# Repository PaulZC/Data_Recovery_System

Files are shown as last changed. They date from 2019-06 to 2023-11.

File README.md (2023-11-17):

# Data_Recovery_System

### ! Still Work In Progress - but more complete than it was !

This is the repository for the SuperBIT Data Recovery System (a.k.a. the data drop capsule).

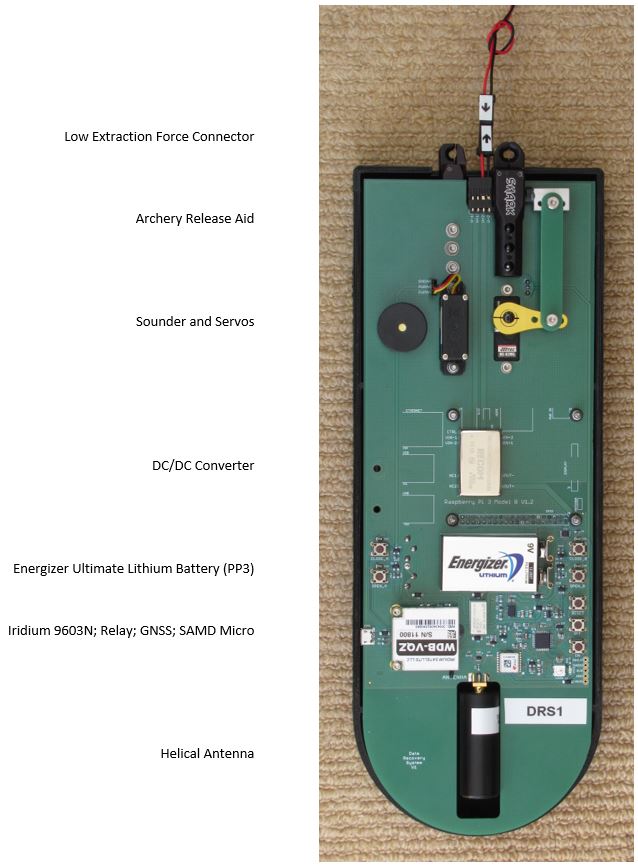
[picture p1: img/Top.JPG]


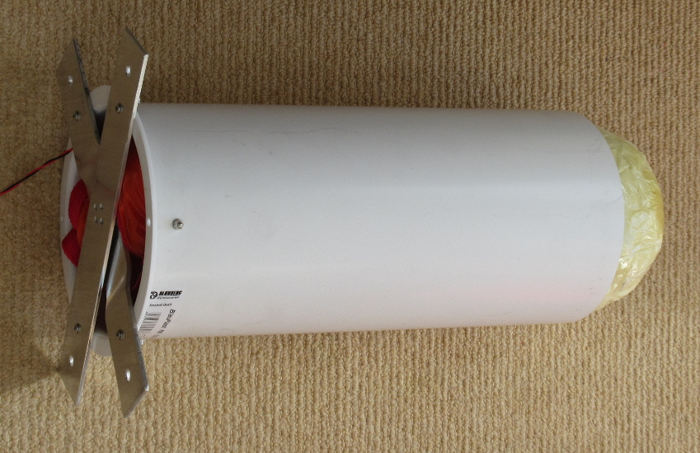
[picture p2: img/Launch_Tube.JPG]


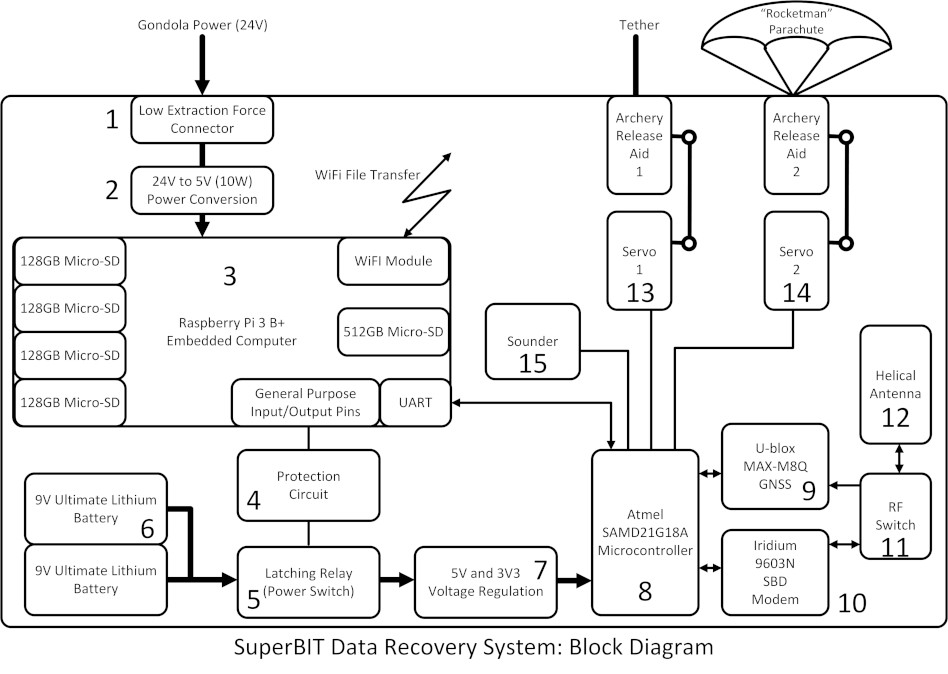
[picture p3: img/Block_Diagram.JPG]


The DRS comprises:
- Raspberry Pi equipped with: 1 x 512GB and 4 x 128GB (RAID1) SD data storage
- ATSAMD21G18 microcontroller as used on the Adafruit Feather M0 Adalogger and the Arduino Zero
- [u-blox MAX-M8Q GNSS receiver](https://www.u-blox.com/en/product/max-m8-series)
- Iridium 9603N Short Burst Data modem
- Maxtena M1600HCT-P-SMA antenna, shared via a Skyworks AS179-92LF RF switch
- two [servo-actuated](https://www.servoshop.co.uk/index.php?pid=HITHS82MG&area=Servo)
[Scott Archery release aids](https://scottarchery.com/collections/releases/products/shark-release): one for the tether and one for the parachute
- [Rocketman 4' parachute](https://the-rocketman.com/recovery-html/)
- Low extraction force power connector
- 3D-printed cover
- PU foam enclosure
- PVC launch tube

See [LEARN.md](./LEARN.md) for more details.

[PCB.md](./PCB.md) contains instructions on how to populate and test the PCB.

[PI.md](./PI.md) contains instructions on how to configure the Raspberry Pi.

[ASSEMBLY.md](./ASSEMBLY.md) contains instructions on how to prepare the DRS for flight.

[GoGoGo.md](./GoGoGo.md) contains instructions on how to release and track the DRS.

The schematic, PCB layout and Bill Of Materials can be found in [Data_Recovery_System_V1.pdf](./Data_Recovery_System_V1.pdf)

The BOM is also available in [Excel .xlsx format](./Data_Recovery_System_BOM.xlsx)

The [Eagle](./Eagle) directory contains the schematic and pcb design files.

The [Arduino](./Arduino) directory contains the Arduino code for the SAMD microcontroller.

The [Drawings](./Drawings) directory contains the drawings for the trigger linkage.

The [OpenSCAD](./OpenSCAD) directory contains the OpenSCAD and STL files for the 3D-printed cover, release crown/mount, and heatsink.

The Python software tools which need to be installed on the Raspberry Pi can be found the [DRS_Python_Tools repo](https://github.com/PaulZC/DRS_Python_Tools).

See [SERVO.md](./SERVO.md) for details on how to modify the HiTec servo for
high altitude operation.

See [SHARK.md](./SHARK.md) for details on how to modify the Scott Archery Shark release aid.

## Licence

This project is distributed under a Creative Commons Attribution + Share-alike (BY-SA) licence.
Please refer to section 5 of the licence for the "Disclaimer of Warranties and Limitation of Liability".

Enjoy!

**_Paul_**

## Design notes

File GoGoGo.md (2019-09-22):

# GoGoGo

Instructions on how to enable, release and track the DRS.

Also included are [instructions](https://github.com/PaulZC/Data_Recovery_System/blob/master/GoGoGo.md#step-10-resetting-the-microcontroller) on how to reset the microcontroller from 'Gone' mode into 'Waiting for GoGoGo' mode (required after performing a drop / test drop).

## Prerequisites

- The DRS should have been prepared following the instructions in [ASSEMBLY.md](https://github.com/PaulZC/Data_Recovery_System/blob/master/ASSEMBLY.md)
- The Raspberry Pi should have been configured for SuperBIT WiFi and have the [DRS_Python_Tools](https://github.com/PaulZC/DRS_Python_Tools) installed following the instructions in [PI.md](https://github.com/PaulZC/Data_Recovery_System/blob/master/PI.md)
- The SAMD microcontroller should have been programmed with the correct Arduino code; the servo open/close positions set and the latching relay set OFF (which is only possible while the Pi is powered)
- The microcontroller code should have been freshly installed. If a test drop has been performed, the code needs to be 'reset' either by re-uploading the code or by following the [instructions below](https://github.com/PaulZC/Data_Recovery_System/blob/master/GoGoGo.md#step-10-resetting-the-microcontroller)

## Step 1: Apply power

- Apply 24V DC power to the DRS via the 2-pin low extraction force connector. The Recom REC10-2405SRWZ/H3/A/M DC-DC converter can operate from 9V to 36V. (A 48V version is available which can operate from 18V to 75V)
- The Raspberry Pi will boot up and attempt to connect to WiFi: SSID SuperBIT with PSK Timmins2019

## Step 2: Log in using SSH

- Connect to the Pi using SSH. Log in as user 'pi' with password 'raspberry'

## Step 3: File transfer

- Transfer files onto the Pi's /mnt/raid1 RAID storage using SFTP

## Step 4: Power up the microcontroller

- A few minutes before the chosen drop time, use the SSH console to cd into the DRS_Python_Tools directory
- Power up the microcontroller by running the script 'DRS_on.py': python DRS_on.py
- The script sets three of the Pi's GPIO pins into the correct state to set the Omron latching relay, switching on 9V battery power to the microcontroller
- The microcontroller will power up and will start to establish a GNSS fix

## Step 5: Check the GNSS fix status

- The NMEA messages from the u-blox MAX-M8Q GNSS receiver are echoed by the microcontroller to the Pi's serial port
- Run the script 'DRS_log_serial.py' from the SSH console: python DRS_log_serial.py
- The script runs for 5 seconds and will append the incoming serial data to DRS_serial_log.txt. The script then displays the tail of the log file
- Look at the lines containing GPGGA. If the GNSS has achieved a fix, you should see the correct date, time, latitude and longitude
- If you only see the correct time, the GNSS receiver has locked onto at least one satellite but has not yet established a fix
- If the GNSS has not established a fix, decide whether to wait for a fix or whether to drop anyway (hoping that the GNSS will establish a fix during the descent - it should!)

## Step 6: Drop

- 30 seconds before the desired drop time, run the script 'DRS_GoGoGo.py': python DRS_GoGoGo.py
- The script will append any incoming GNSS serial data to DRS_serial_log.txt for three seconds; the script then displays the tail of the log file
- The script then sends a GoGoGo command to the microcontroller via the serial port
- The script then shuts down the Pi (sudo shutdown now)
- The microcontroller will wait 30 seconds and then open archery release A
- The sounder will start to beep every 5 seconds

## Step 7: During the descent

- The DRS will fall, pulling apart the power connection (disconnecting power to the Pi)
- The parachute will unfurl but will remain attached to archery release B
- The microcontroller is now in 'Gone' mode
- The microcontroller will obtain a GNSS fix and send this as an Iridium Short Burst Data message every 2 minutes
- Messages will be delivered via email to the addresses configured in the Rock7 Operations Delivery Groups
- The message interval can be changed by logging in to RockBLOCK Operations (https://rockblock.rock7.com/Operations) (ask Paul for the username and password) and using the 'Send a Message' option
- Send a message to the RockBLOCK (DRS1 is RockBLOCK 11800) containing the text: [INTERVAL=nn]
- where nn is the message interval in minutes. The square brackets are important
- If you want to try this as a test, make sure you do it outdoors where the DRS has a clear view of the sky
- The [Iridium_9603_Beacon webpage](https://github.com/PaulZC/Iridium_9603_Beacon/blob/master/RockBLOCK.md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) provides extra information

## Step 8: After landing

- Once you have confirmed that the DRS has landed, you can release it from the parachute via an Iridium message
- Send a message containing the text: [PARACHUTE=hh:mm]
- where hh and mm are the current **UTC** time. The square brackets are important
- The microcontroller will ignore the message if hh and mm do not match current UTC time to +/- 15 minutes. This ensures any old queued messages are ignored
- The microcontroller will open archery release B after the next SBD message cycle

## Step 9: Other commands

- If you wish to disable the sounder / beeper, send the message: [SOUNDER_OFF]
- The sounder can be re-enabled with the message: [SOUNDER_ON]
- The DRS can also be configured to forward all messages to another RockBLOCK using the message: [RBDESTINATION=nnnnn]
- where nnnnn is the RockBLOCK serial number (not the IMEI) of the 9603N you wish the messages to be forwarded to
- Full details can be found on the [Iridium_9603_Beacon webpage](https://github.com/PaulZC/Iridium_9603_Beacon/blob/master/RockBLOCK.md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)
- The recovery team could use this to track the DRS and release the parachute from anywhere - [without an internet connection](https://github.com/PaulZC/Iridium_9603_Beacon/blob/master/RockBLOCK.md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)

## Step 10: Resetting the microcontroller

- Once the microcontroller has received a 'GoGoGo' message, a 'Gone' flag is set in flash memory. Resetting the microcontroller or disconnecting and reconnecting the batteries does not clear the flag
- To reset the microcontroller into 'Waiting for Go' mode: press and hold the OPEN_A, CLOSE_A, OPEN_B and CLOSE_B buttons, then press and release the RESET button
- Keep the OPEN_A, CLOSE_A, OPEN_B and CLOSE_B buttons pressed down until the NeoPixel goes green, then release them
- The 'Gone' flag is now clear. The microcontroller returns to [Step 5](https://github.com/PaulZC/Data_Recovery_System/blob/master/GoGoGo.md#step-5-check-the-gnss-fix-status)

## Step 11: Resetting the latching relay

- Resetting the latching relay can only be done while the Pi is powered
- Connect the DRS to 24V using the power pins
- The OFF button can then be pressed which resets (opens) the latching relay contacts
- To be kind to the Pi, SSH in over WiFi or Ethernet and 'sudo shutdown now' before disconnecting the power

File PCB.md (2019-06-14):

# PCB Assembly

This guide contains instructions on how to assemble the DRS PCB: starting with the bare PCB and finishing with a populated PCB which has been tested with test code.

### Blank PCB

Start by having the blank PCBs manufactured. If you are based in the UK or Europe, I can recommend
[Multi-CB](https://www.multi-circuit-boards.eu/en/index.html) who can manufacture PCBs in 1-8 working days and
can process the Eagle .brd file direct - there's no need to generate Gerber files.

You will find the PCB and paste stencil design files in the [Eagle directory](https://github.com/PaulZC/Data_Recovery_System/tree/master/Eagle)

The PCB and trigger linkage pieces are incorporated into a single board. The design includes two score lines which Multi-CB
will machine into the board if you ask them to, allowing the trigger linkage pieces to be easily snapped off.

My recommended options are:
- Layers: 4 layers
- Format: Panel
- Panel Type: Multiplier
- Mechanical treatment: Milled and Scored
- Panelization: Yes, by Multi-CB
- Panel size (x/y): 128.27 X 304.8 mm
- Piece size (x/y): 128.27 X 304.8 mm
- PCBs / x-, y-Axis: 1 X 1 Pieces
- Surface finish: Chemical gold (ENIG)
- Material: FR4, 1.55mm
- Cu layers: 35um
- Solder stop: both sides, green
- Marking print: both sides, white
- **Comments: PCB includes two score lines. VSCORE data is in layer 148**

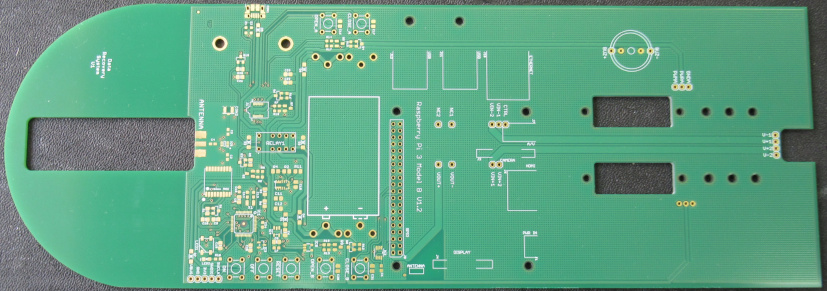
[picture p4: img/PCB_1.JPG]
PCB_1


### Add solder paste

Multi-CB can also provide you with a solder paste (SMD) stencil for the PCB. The [Eagle directory](https://github.com/PaulZC/Data_Recovery_System/tree/master/Eagle)
contains a separate design for the paste stencil which is 10mm wider than the DRS PCB, to allow you to fix it down with tape.

My recommended options are:
- SMD stencil for: top layer
- Size (x/y): 118.11 X 88.9 mm
- Type: custom
- Pad reduction: yes, 10%
- Thickness: 100um
- Existing fiducials: lasered through
- Text type: half lasered
- Double-sided brushing: yes

Secure the blank PCB onto a flat work surface by locating it between two engineer's squares. I use a sheet of toughened glass
as the work surface as it is both very flat and easy to clean.

Use the two round fiducials to line up the stencil with the PCB. Secure the stencil with tape.

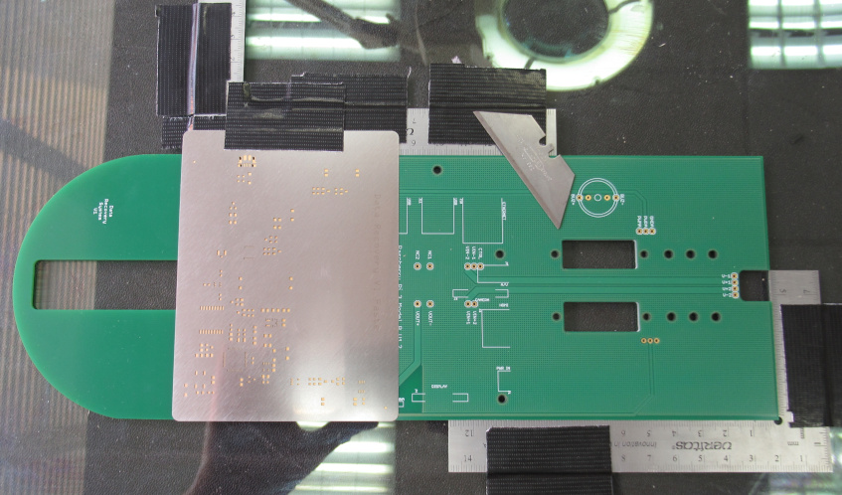
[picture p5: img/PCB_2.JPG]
PCB_2


Apply solder paste close to the component cut-outs and then scrape the paste over the stencil using a knife blade
or a similar straight edge. Take appropriate safety precautions when working with solder paste - particularly if you are using
tin-lead solder instead of lead-free.

### Position the surface mount components

Position the components onto the blobs of solder paste using tweezers. A magnifier lamp or a USB microscope will
help you place the components in the correct position. J1 - the 20-way Samtec connector - is probably the trickiest
component to position. Take extra time to make sure the legs are centered accurately on the pads.

### Reflow the surface mount components

Use a reflow oven to heat the circuit board to the correct temperatures to melt the solder. A reflow oven doesn't need to be
expensive. The one shown below was assembled from:

- Quest 9L 800W mini-oven
- Inkbird PID temperature controller and 40A solid state relay
- Type K thermocouple

Several people have published good reflow oven construction guides, including [this one](http://tt7hab.blogspot.com/2018/06/the-reflow-oven.html) and [this one](http://www.die4laser.com/toaster/index.html).

V5_Assembly_8

Use the correct temperature profile for your solder paste, but you won't go far wrong with 160C for four minutes, followed by
210C for one minute, followed by a cool-down with the door open. Use a flashlight to check that the solder has melted across
the whole PCB at 210C. Hold the temperature at 210C a little longer if some of the solder paste still appears 'gray' instead of 'silver'.

### Check for shorts

Carefully examine all the solder joints and correct any shorts you find.

The 'trick' to removing a short is to add more solder or solder paste and then to use
copper solder braid or wick to remove all the solder in one go.

Shorts_1

Shorts_2

Shorts_3

Use a cotton bud (q-tip) dipped in Iso-Propyl Alcohol (IPA / Propanol / rubbing alcohol) to remove any flux residue.

All being well, your PCB should look like this:

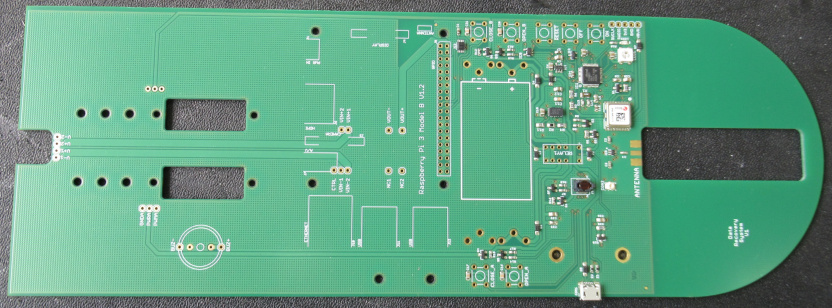
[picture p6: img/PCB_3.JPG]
PCB_3


### Press-in nuts

The Iridium 9603N module is held in place by two 2-56 screws. The threaded 2-56 press-in nuts now need to be pressed into the rear of the
PCB. These are McMaster part number 95117A411. The nuts are best pressed into place using an arbor press.

### Add the non-surface mount components

The non-surface mount components (battery clips, relay, switches, SMA conector, DC-DC converter, sounder 3-pin servo headers, 4-pin power header) can now be soldered in by hand.

### Install the bootloader

The SAMD21G18A processor now needs to be configured with a bootloader using a J-Link programmer or similar, connecting it to the five pads on the right hand edge of the PCB.
Full details are included in the [Iridium_9603_Beacon repo](https://github.com/PaulZC/Iridium_9603_Beacon/blob/master/LEARN.md#how-do-i-install-the-atsamd21g18-bootloader).

### Test the PCB

Before connecting the Iridium 9603N, it is a good idea to test the completed PCB. The [Arduino](https://github.com/PaulZC/Data_Recovery_System/tree/master/Arduino)
directory contains a sketch called Data_Recovery_System_V1_Test.ino which will test all of the components on the PCB for you. Messages are displayed
on the Arduino IDE Serial Monitor as each test is passed.

### Install the Iridium 9603N module

Take appropriate ESD precautions throughout and especially when handling the 9603N module.

Connect the 9603N to the beacon PCB using a HIROSE (HRS) u.FL-u.FL cable or similar. The cable needs to be 50 Ohm and approximately 25mm long.

Carefully fold the 9603N module over onto the PCB, insert the 20-way connector into the Samtec socket, then secure the module using:
- two 4.5mm OD x 6mm spacers (McMaster 94669A100)
- two 2-56 x 7/16" screws (McMaster 92185A081)

Screw the GNSS+Iridium antenna onto the SMA connector

### Retest the PCB

Now that the 9603N has been installed, retest the completed PCB using the [Arduino test code](https://github.com/PaulZC/Data_Recovery_System/tree/master/Arduino/Data_Recovery_System_V1_Test).

### Secure J1 with Epoxy

I recommend securing J1 to the PCB with a small amount of epoxy to make it more robust. 3M Scotch-Weld 2216 is an ideal choice as it remains slightly flexible when cured.
You will need to temporarily remove the 9603N while you apply the epoxy. Apply the mixed epoxy around the body and legs of J1 using a toothpick,
taking great care to keep the epoxy clear of the connector opening and pins. Make sure the epoxy is fully cured before re-installing the 9603N.

### Lacquer the PCB

I recommend giving the PCB a coat of lacquer. You will need to temporarily remove the 9603N while you apply the lacquer. Cover all of the surface mount components with
[Acrylic Protective Lacquer (conformal coating)](https://uk.rs-online.com/web/p/conformal-coatings/3217324/) avoiding J1, CON1, CON2, the switches and IO pads.

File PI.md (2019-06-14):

# Raspberry Pi Configuration

This guide contains instructions on how to configure the Raspberry Pi for use on the DRS.

1. Burn the latest Raspberry Pi Raspbian onto the 512GB micro SD card
- Visit https://www.raspberrypi.org/downloads/
- Download the latest "Raspbian Stretch with desktop and recommended software"
- Extract the .img with e.g. http://www.7-zip.org/download.html
- Burn it to the SD card using e.g. https://sourceforge.net/projects/win32diskimager/

2. Insert the SD card into a Raspberry Pi 3 B+
- Connect screen, mouse, keyboard and (finally) power

3. Let the Pi boot. It will automatically resize the SD card file system to its full size

4. Go through the set up process to set the country and connect to a WiFi network

5. Skip the update software step (we’ll be doing an update and upgrade shortly)

6. Let the Pi restart if requested

7. Open a terminal window by clicking on the >_ icon

8. In  the terminal window:
- sudo raspi-config
- Select option2 then option N1 to change the hostname to e.g. drs1
- Select option 3 then option B1 then option B2 to boot into “Console Autologin”
- Select option 4 then option I4 to change the WiFi country if required
- Select option 5 then option P2, select Yes to enable the SSH server
- Select option 5 then option P6, select No for the login shell over serial, then select Yes to enable the hardware serial port
- Select finish and reboot the Pi

9. After the reboot, you should be presented with a console prompt (e.g.) pi@drs1

10. (You can start an X session if you want to using startx)

11. Remove Wolfram and LibreOffice to free up some storage space
- sudo apt-get purge wolfram-engine
- sudo apt-get clean
- sudo apt-get autoremove
- sudo apt-get remove --purge libreoffice*
- sudo apt-get clean
- sudo apt-get autoremove

12. Update and upgrade raspbian
- sudo apt-get update
- sudo apt-get upgrade

13. If you want to change WiFi networks from the console, you can do this by editing wpa_supplicant.conf
- sudo nano /etc/wpa_supplicant/wpa_supplicant.conf

14. Make a note of the Pi’s wireless (wlan0) IP number (hopefully it won’t change when you reboot)
- ifconfig -a

15. Shutdown the Pi
- sudo shutdown now

16. Wait until the green LED stops blinking, then remove the power

17. Disconnect the screen, keyboard and mouse

18. Install the four 128GB micro-SD cards in their miniature USB adapters

19. Power the Pi and you should see LEDs light up on all four micro-SD adapters

20. Connect to the Pi over SSH using (e.g.) PuTTY
- https://www.chiark.greenend.org.uk/~sgtatham/putty/latest.html
- Log in as user pi with the password raspberry (unless you changed it!)

21. Run lsblk and check that you now have four drives called sda, sdb, sdc and sdd. (The 512GB card is called mmcblk0)

22. Create a RAID-1 system following the instructions in section 3 of:
- https://blog.alexellis.io/hardened-raspberry-pi-nas/ 
- sudo fdisk /dev/sda
- o
- n
- p
- enter (default)
- enter (default)
- enter (default)
- w
- sudo fdisk /dev/sdb
- o
- n
- p
- enter (default)
- enter (default)
- enter (default)
- w
- sudo fdisk /dev/sdc
- o
- n
- p
- enter (default)
- enter (default)
- enter (default)
- w
- sudo fdisk /dev/sdd
- o
- n
- p
- enter (default)
- enter (default)
- enter (default)
- w
- sudo apt-get -qy install mdadm
- sudo mdadm --create --verbose /dev/md0 --level=mirror --raid-devices=4 /dev/sda1 /dev/sdb1 /dev/sdc1 /dev/sdd1
- y
- sudo mkdir -p /mnt/raid1
- sudo mkfs.ext4 /dev/md0
- sudo mount /dev/md0 /mnt/raid1/
- echo "/dev/md0  /mnt/raid1/ ext4 defaults,noatime 0 1" | sudo tee -a /etc/fstab
- sudo mdadm --detail --scan | sudo tee -a /etc/mdadm/mdadm.conf
- sudo reboot

23. Let the Pi reboot then connect again with PuTTY

24. Check that the RAID drive is ok
- df /mnt/raid1
- should return something like:
- Filesystem     1K-blocks     Used    Available Use% Mounted on
- /dev/md0       122317432 61464 115999484   1% /mnt/raid1

25. When we mount the Pi onto the DRS, it is going to be difficult to connect either screen, mouse and keyboard or to go in over WiFi (if you need to connect to a new WiFi network). So, we’ll set up a static IP address and DHCP server on the Ethernet port so we can SSH in through that. Your WiFi is probably using 192.168.0.n addresses, so we’ll use 192.168.1.n addresses for Ethernet
- sudo nano /etc/dhcpcd.conf
- uncomment and change the two lines below “Example static IP configuration:”
- interface eth0
- static ip_address=192.168.1.2/24
- ctrl-x
- y
- enter

26. Install dnsmasq:
- sudo apt-get install dnsmasq

27. Create a new dnsmasq.conf file:
- sudo mv /etc/dnsmasq.conf /etc/dnsmasq.conf.orig
- sudo nano /etc/dnsmasq.conf
- interface=eth0
- dhcp-range=192.168.1.3,192.168.1.20,255.255.255.0,24h
- ctrl-x
- y
- enter

28. Reload dnsmasq:
- sudo systemctl reload dnsmasq

29. Check the Ethernet connection by SSH-ing in over Ethernet. The Pi is 192.168.1.2

30. Download the Python tools which will enable the Arduino part of the DRS, copy the incoming GNSS serial data to DRS_serial_log.txt, and tell the DRS to “GoGoGo”:
- git clone https://github.com/PaulZC/DRS_Python_Tools

31. We now need to make DRS_Python_Tools/DRS_tx_off.py run on startup to correct Paul’s booboo. The serial Tx pin can provide just enough power to try and start the SAMD processor. DRS_tx_off.py prevents this by making the Tx pin low. DRS_on.py has to put the Tx pin back into alt5 mode before we can use the serial port again.
- sudo nano /etc/profile
- scroll to the end of the file and add
- sudo python /home/pi/DRS_Python_Tools/DRS_tx_off.py
- ctrl-x
- y
- enter

32. Shutdown the Pi. Disconnect the power once the green LED has stopped flashing. The LEDs on the four micro-SD card adapters should also stop flashing.
- sudo shutdown now

33. You can now bolt the Pi to the DRS circuit board.

The [DRS_Python_Tools repo](https://github.com/PaulZC/DRS_Python_Tools) contains:

**DRS_tx_off.py** pulls the Pi’s serial Tx pin low to prevent it from supplying power to the SAMD processor. This now runs automatically on boot.

**DRS_on.py** will set the latching relay so it provides power to the SAMD processor and restores the serial Tx pin to alt5 mode.

**DRS_log_serial.py** runs for 5 seconds, appends any serial data to DRS_serial_log.txt and then shows the tail of the log file so you can see if the GNSS receiver has established a fix.

**DRS_GoGoGo.py** sends the Go command to the SAMD processor. Confirm with y or Y. The drop will take place after 30 seconds (allowing time for the Pi to shutdown).

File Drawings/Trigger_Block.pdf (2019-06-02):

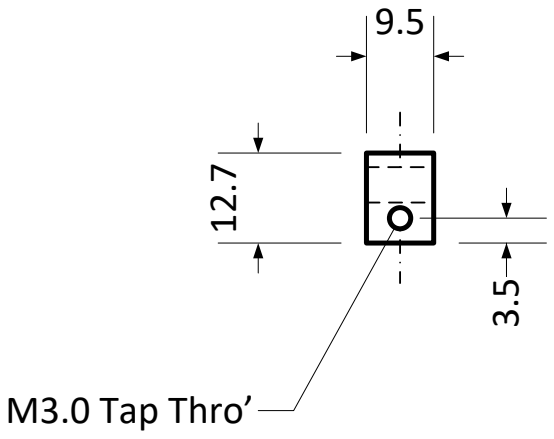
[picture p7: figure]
M3.0 Tap Thro’

Trigger Block

(Revised version for Shark and Little Goose)

Aluminium
(1/2" x 3/8" bar cut into 3/8" lengths)

Qty: 20

Ø5.0

9.5

4.5

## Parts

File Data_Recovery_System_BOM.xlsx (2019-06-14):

Part | X | Y | Angle | Package | Value | Manufacturer | Manufacturer Part No | Farnell Part No | Mouser Part No | McMaster Part No | Description | Alternative Part
Dimensions | 107.95 | 304.80 |  |  |  |  |  |  |  |  | Excludes snap-off servo linkage pieces
Fiducials - for solder paste mask alignment:
FD1 | 3.28 | 71.12 | 0 |  |  |  |  |  |  |  | Fiducial 1mm
FD2 | 102.75 | 149.86 | 0 |  |  |  |  |  |  |  | Fiducial 1mm
Surface Mount Components:
C1 | 100.2 | 141.22 | 0 | 0603 | 1uF | Walsin | 0603X105K100CT | 2496916 |  |  | MultiLayer Ceramic Capacitor; 1uF; 10V; 0603; X5R | 1uF 50V ±10% 0603 Samsung
C2 | 58.93 | 83.57 | 0 | 0603 | 120pF | Walsin | 0603B121K500CT | 2524820 |  |  | MultiLayer Ceramic Capacitor; 120pF; 50V; 0603
C3 | 49.4 | 83.57 | 180 | 0603 | 120pF | Walsin | 0603B121K500CT | 2524820 |  |  | MultiLayer Ceramic Capacitor; 120pF; 50V; 0603
C4 | 53.98 | 77.98 | 90 | 0603 | 120pF | Walsin | 0603B121K500CT | 2524820 |  |  | MultiLayer Ceramic Capacitor; 120pF; 50V; 0603
C5 | 74.8 | 88.27 | 180 | 0805 | 0.1uF | Walsin | 0805B104K500CT | 2496944 |  |  | MultiLayer Ceramic Capacitor; 0.1uF; 50V; 0805; X7R | 100nF 50V ±10% 0805 Samsung
C6 | 87.1 | 105.54 | 0 | 0805 | 10uF | Walsin | 0805F106Z100CT | 2496998 |  |  | MultiLayer Ceramic Capacitor; 10uF; 10V; 0805 | 10uF 16V ±10% 0805 Samsung
C7 | 92.75 | 102.39 | 270 | 0603 | 1uF | Walsin | 0603X105K100CT | 2496916 |  |  | MultiLayer Ceramic Capacitor; 1uF; 10V; 0603; X5R | 1uF 50V ±10% 0603 Samsung
C8 | 90.53 | 102.39 | 270 | 0805 | 10uF | Walsin | 0805F106Z100CT | 2496998 |  |  | MultiLayer Ceramic Capacitor; 10uF; 10V; 0805 | 10uF 16V ±10% 0805 Samsung
C9 | 82.2 | 79.86 | 270 | 0805 | 0.1uF | Walsin | 0805B104K500CT | 2496944 |  |  | MultiLayer Ceramic Capacitor; 0.1uF; 50V; 0805; X7R | 100nF 50V ±10% 0805 Samsung
C10 | 82.26 | 75.84 | 90 | 0805 | 10uF | Walsin | 0805F106Z100CT | 2496998 |  |  | MultiLayer Ceramic Capacitor; 10uF; 10V; 0805 | 10uF 16V ±10% 0805 Samsung
C11 | 74.4 | 102.87 | 90 | 0805 | 10nF | Walsin | 0805B103K500CT | 2496939 |  |  | MultiLayer Ceramic Capacitor; 10nF; 50V; 0805; X7R | 10nF 50V ±5% 0805 Samsung
C12 | 78.21 | 102.87 | 90 | 0805 | 10uF | Walsin | 0805F106Z100CT | 2496998 |  |  | MultiLayer Ceramic Capacitor; 10uF; 10V; 0805 | 10uF 16V ±10% 0805 Samsung
C13 | 73.03 | 93.6 | 180 | 0603 | 12pF | Walsin | 0603N120J500CT | 2496884 |  |  | MultiLayer Ceramic Capacitor; 12pF; 50V; 0603 | 12pF 50V ±5% 0603 Samsung
C14 | 73.03 | 91.31 | 180 | 0603 | 12pF | Walsin | 0603N120J500CT | 2496884 |  |  | MultiLayer Ceramic Capacitor; 12pF; 50V; 0603 | 12pF 50V ±5% 0603 Samsung
C15 | 69.19 | 109.22 | 0 | 0805 | 10uF | Walsin | 0805F106Z100CT | 2496998 |  |  | MultiLayer Ceramic Capacitor; 10uF; 10V; 0805 | 10uF 16V ±10% 0805 Samsung
C16 | 7.62 | 125.2 | 0 | 0805 | 10nF | Walsin | 0805B103K500CT | 2496939 |  |  | MultiLayer Ceramic Capacitor; 10nF; 50V; 0805; X7R | 10nF 50V ±5% 0805 Samsung
C17 | 7.62 | 137.9 | 0 | 0805 | 10nF | Walsin | 0805B103K500CT | 2496939 |  |  | MultiLayer Ceramic Capacitor; 10nF; 50V; 0805; X7R | 10nF 50V ±5% 0805 Samsung
C18 | 71.12 | 88.27 | 180 | 0603 | 1uF | Walsin | 0603X105K100CT | 2496916 |  |  | MultiLayer Ceramic Capacitor; 1uF; 10V; 0603; X5R | 1uF 50V ±10% 0603 Samsung
C19 | 91.89 | 81.69 | 0 | 0805 | 10uF | Walsin | 0805F106Z100CT | 2496998 |  |  | MultiLayer Ceramic Capacitor; 10uF; 10V; 0805 | 10uF 16V ±10% 0805 Samsung
C20 | 100.33 | 125.2 | 0 | 0805 | 10nF | Walsin | 0805B103K500CT | 2496939 |  |  | MultiLayer Ceramic Capacitor; 10nF; 50V; 0805; X7R | 10nF 50V ±5% 0805 Samsung
C21 | 100.33 | 137.9 | 0 | 0805 | 10nF | Walsin | 0805B103K500CT | 2496939 |  |  | MultiLayer Ceramic Capacitor; 10nF; 50V; 0805; X7R | 10nF 50V ±5% 0805 Samsung
C22 | 30.48 | 105.69 | 270 | 0805 | 10uF | Walsin | 0805F106Z100CT | 2496998 |  |  | MultiLayer Ceramic Capacitor; 10uF; 10V; 0805 | 10uF 16V ±10% 0805 Samsung
C23 | 27.3 | 105.69 | 270 | 0805 | 0.1uF | Walsin | 0805B104K500CT | 2496944 |  |  | MultiLayer Ceramic Capacitor; 0.1uF; 50V; 0805; X7R | 100nF 50V ±10% 0805 Samsung
C24 | 84.2 | 97.16 | 0 | 0603 | 1uF | Walsin | 0603X105K100CT | 2496916 |  |  | MultiLayer Ceramic Capacitor; 1uF; 10V; 0603; X5R | 1uF 50V ±10% 0603 Samsung
C25 | 92.71 | 92.84 | 0 | 0805 | 10uF | Walsin | 0805F106Z100CT | 2496998 |  |  | MultiLayer Ceramic Capacitor; 10uF; 10V; 0805 | 10uF 16V ±10% 0805 Samsung
C26 | 28.45 | 87.63 | 270 | 0805 | 10uF | Walsin | 0805F106Z100CT | 2496998 |  |  | MultiLayer Ceramic Capacitor; 10uF; 10V; 0805 | 10uF 16V ±10% 0805 Samsung
CON1 | 2.99 | 92.71 | 270 |  | Micro_USB | Amphenol_FCI | 10103594 | 2293752 |  |  | Amphenol FCI 10103594 Micro USB Type B | A01SB7X4X1B21-167 Micro USB 5S B
CON2 | 41.78 | 83.57 | 0 | uFL | uFL | Hirose | U.FL-R-SMT(01) | 3908021 |  |  | HIROSE U.FL-R-SMT(01); U.FL Coaxial; Straight Jack; 50 ohm
D1 | 82.18 | 105.57 | 180 | SOD-123 | MBR120 | ON SEMICONDUCTOR | MBR120VLSFT1G | 1431044 |  |  | Schottky Rectifier; 20V; 1A; SOD-123
D2 | 53.34 | 91.44 | 180 | SOD-123 | MBR120 | ON SEMICONDUCTOR | MBR120VLSFT1G | 1431044 |  |  | Schottky Rectifier; 20V; 1A; SOD-123
D3 | 53.34 | 111.76 | 180 | SOD-123 | MBR120 | ON SEMICONDUCTOR | MBR120VLSFT1G | 1431044 |  |  | Schottky Rectifier; 20V; 1A; SOD-123
D4 | 81.41 | 110.87 | 0 | SOD-123 | MBR120 | ON SEMICONDUCTOR | MBR120VLSFT1G | 1431044 |  |  | Schottky Rectifier; 20V; 1A; SOD-123
D5 | 10.16 | 93.98 | 180 | SOD-123 | MBR120 | ON SEMICONDUCTOR | MBR120VLSFT1G | 1431044 |  |  | Schottky Rectifier; 20V; 1A; SOD-123
D6 | 25.4 | 111.76 | 180 | SOD-123 | MBR120 | ON SEMICONDUCTOR | MBR120VLSFT1G | 1431044 |  |  | Schottky Rectifier; 20V; 1A; SOD-123
D7 | 95.89 | 70.99 | 0 | SOD-123 | MBR120 | ON SEMICONDUCTOR | MBR120VLSFT1G | 1431044 |  |  | Schottky Rectifier; 20V; 1A; SOD-123
IC1 | 83.82 | 90.17 | 0 | TQFP48-7X7 | SAMD21G18A-AFT | Atmel / Microchip | SAMD21G18A-AFT |  | 556-ATSAMD21G18A-AFT
IC2 | 94.49 | 140.34 | 0 | SOP65P400X130-8N | SN74LVC2G02DCTR | Texas Instruments | SN74LVC2G02DCTR | 1236358 |  |  | NOR Gate, 2 Input, 32 mA, 1.65 V to 5.5 V, SSOP-8
IC3 | 91.66 | 96.91 | 0 | SOT23-3 | MCP111T-240E/TT | Microchip | MCP111T-240E/TT | 1627192 |  |  | Reset Supervisor; SOT23-3; 2.40V; Open Drain; Active Low
IC4 | 86.72 | 102.39 | 270 | SOT23-5 | SPX3819-3.3 | Exar | SPX3819M5-L-3-3/TR |  | 701-SPX3819M5-L-33TR |  | LDO Voltage Regulator; 500mA; SOT-23-5
IC5 | 53.98 | 82.42 | 270 | SOT65P220X100-6N | AS179-92LF | Skyworks Solutions | AS179-92LF | 1753762 | 873-AS179-92LF |  | Skyworks AS179-92LF RF Switch
IC6 | 68.15 | 80.34 | 0 |  | MAX-M8Q | u-blox | MAX-M8Q |  |  |  | https://www.u-blox.com/en/product/max-m8-series
IC7 | 69.32 | 104.32 | 0 | QFN-20 | MPM3610 | MPS | MPM3610AGQV-P |  | 946-MPM3610AGQV-P |  | Switching Voltage Regulator; 21V; 1.2A; DC/DC
IC8 | 92.61 | 114.18 | 0 | SOT23-5 | 74AHCT1G125DBV | Texas Instruments | SN74AHCT1G125DBVR | 1105927 |  |  | Buffer / Line Driver; Single Gate
IC9 | 90.55 | 109.34 | 180 | SOT23-5 | 74AHCT1G125DBV | Texas Instruments | SN74AHCT1G125DBVR | 1105927 |  |  | Buffer / Line Driver; Single Gate
J1 | 41.09 | 94.65 | 270 |  | SS4-10-3.50 | Samtec | SS4-10-3.50-L-D-K-TR | 2085336 |  |  | Samtec SS4-10-3.50-L-D-K-TR
LED1 | 91.8 | 76.52 | 0 |  | WS2812B | Sparkfun / Worldsemi | WS2812B |  | 474-COM-13667 |  | RGB LED with Driver
LED2 | 96.88 | 76.71 | 180 | 2.0x1.25 | RED | Wurth Electronik | 150080RS75000 | 2322077 | 710-150080RS75000 |  | LED; Red; 20mA; 2V; 2.0x1.25mm
Q1 | 79.03 | 79.8 | 0 | SOT23 | DMG3415U-7 | Diodes Inc. | DMG3415U-7 | 1843688 |  |  | MOSFET; P Channel; SOT23-WIDE
Q2 | 65.15 | 92.08 | 180 | SOT23 | 2N2222 | Fairchild | MMBT2222A | 9846700 |  |  | Bipolar (BJT) Single Transistor, NPN, 40 V, 350 mW, 1 A
Q3 | 60.96 | 89.28 | 180 | SOT23 | DMG3415U-7 | Diodes Inc. | DMG3415U-7 | 1843688 |  |  | MOSFET; P Channel; SOT23-WIDE
Q4 | 15.39 | 132.49 | 0 | SOT23 | DMG3415U-7 | Diodes Inc. | DMG3415U-7 | 1843688 |  |  | MOSFET; P Channel; SOT23-WIDE
Q5 | 15.31 | 125.13 | 0 | SOT23 | 2N2222 | Fairchild | MMBT2222A | 9846700 |  |  | Bipolar (BJT) Single Transistor, NPN, 40 V, 350 mW, 1 A
Q6 | 35.54 | 102.23 | 180 | SOT23 | DMG3415U-7 | Diodes Inc. | DMG3415U-7 | 1843688 |  |  | MOSFET; P Channel; SOT23-WIDE
Q7 | 40.36 | 105.79 | 0 | SOT23 | 2N2222 | Fairchild | MMBT2222A | 9846700 |  |  | Bipolar (BJT) Single Transistor, NPN, 40 V, 350 mW, 1 A
Q8 | 92.43 | 130.05 | 180 | SOT23 | DMG3415U-7 | Diodes Inc. | DMG3415U-7 | 1843688 |  |  | MOSFET; P Channel; SOT23-WIDE
Q9 | 92.43 | 125.1 | 0 | SOT23 | 2N2222 | Fairchild | MMBT2222A | 9846700 |  |  | Bipolar (BJT) Single Transistor, NPN, 40 V, 350 mW, 1 A
Q10 | 21.59 | 87.63 | 90 | SOT23 | DMG3415U-7 | Diodes Inc. | DMG3415U-7 | 1843688 |  |  | MOSFET; P Channel; SOT23-WIDE
R1 | 79.15 | 76.62 | 180 | 0805 | 100K | Multicomp | MC01W08051100K | 9332405 |  |  | Chip Resistor; Thick Film; 100k; 150V; 0805; 100mW | 100K ±1% 0805 RoyalOhm
R2 | 64.24 | 105.79 | 270 | 0805 | 19K1_0.1% | Panasonic | ERA6ARB1912V | 2094729 |  |  | Resistor, Thin Film, 19K1, 0.1%, 0.125W, 0805
R3 | 71.9 | 97.76 | 180 | 0805-NO | 330K | Multicomp | MCWR08X3303FTL | 2447637 |  |  | Chip Resistor; Thick Film; 330k; 150V; 0805; 125mW
R4 | 64.24 | 101.6 | 270 | 0805 | 100K_1% | Panasonic | ERJ6ENF1003V | 2303757 |  |  | Resistor, Thick Film, 100K, 1% 0.125W, 0805
R5 | 60.96 | 92.2 | 180 | 0805-NO | 10K | Multicomp | MC01W0805510K | 9333720 |  |  | Chip Resistor; Thick Film; 10k; 150V; 0805; 100mW
R6 | 76.37 | 97.76 | 180 | 0805 | 100k | Multicomp | MC01W08051100K | 9332405 |  |  | Chip Resistor; Thick Film; 100k; 150V; 0805; 100mW | 100K ±1% 0805 RoyalOhm
R7 | 39.48 | 101.73 | 90 | 0603 | 1K | Multicomp | MCWR06X1001FTL | 2447272 |  |  | Chip Resistor; Thick Film; 1k; 50V; 0603; 100mW | 1K ±1% 0603 RoyalOhm
R8 | 66.42 | 95.89 | 270 | 0603 | 1K | Multicomp | MCWR06X1001FTL | 2447272 |  |  | Chip Resistor; Thick Film; 1k; 50V; 0603; 100mW | 1K ±1% 0603 RoyalOhm
R9 | 64.26 | 95.89 | 270 | 0603 | 10K | Multicomp | MCWR06X1002FTL | 2447230 |  |  | Chip Resistor; Thick Film; 10k; 50V; 0603; 100mW | 10K ±1% 0603 RoyalOhm
R10 | 96.85 | 80.93 | 270 | 0603 | 2.2K | Multicomp | MCWR06X2201FTL | 2447320 |  |  | Chip Resistor; Thick Film; 2.2k; 50V; 0603; 100mW
R11 | 64.24 | 109.98 | 270 | 0805 | 68K | Multicomp | MCWR08X6802FTL | 2447706 |  |  | Resistor, Thick Film, 68K, 1%, 0.125W
R12 | 92.31 | 133.22 | 0 | 0603 | 10K | Multicomp | MCWR06X1002FTL | 2447230 |  |  | Chip Resistor; Thick Film; 10k; 50V; 0603; 100mW | 10K ±1% 0603 RoyalOhm
R13 | 93.45 | 120.9 | 90 | 0603 | 10K | Multicomp | MCWR06X1002FTL | 2447230 |  |  | Chip Resistor; Thick Film; 10k; 50V; 0603; 100mW | 10K ±1% 0603 RoyalOhm
R14 | 14.33 | 121.09 | 90 | 0603 | 1K | Multicomp | MCWR06X1001FTL | 2447272 |  |  | Chip Resistor; Thick Film; 1k; 50V; 0603; 100mW | 1K ±1% 0603 RoyalOhm
R15 | 15.45 | 129.35 | 180 | 0603 | 10K | Multicomp | MCWR06X1002FTL | 2447230 |  |  | Chip Resistor; Thick Film; 10k; 50V; 0603; 100mW | 10K ±1% 0603 RoyalOhm
R16 | 35.54 | 105.41 | 0 | 0603 | 10K | Multicomp | MCWR06X1002FTL | 2447230 |  |  | Chip Resistor; Thick Film; 10k; 50V; 0603; 100mW | 10K ±1% 0603 RoyalOhm
R17 | 16.3 | 121.09 | 90 | 0603 | 10K | Multicomp | MCWR06X1002FTL | 2447230 |  |  | Chip Resistor; Thick Film; 10k; 50V; 0603; 100mW | 10K ±1% 0603 RoyalOhm
R18 | 41.38 | 101.73 | 90 | 0603 | 10K | Multicomp | MCWR06X1002FTL | 2447230 |  |  | Chip Resistor; Thick Film; 10k; 50V; 0603; 100mW | 10K ±1% 0603 RoyalOhm
R19 | 91.55 | 120.9 | 90 | 0603 | 1K | Multicomp | MCWR06X1001FTL | 2447272 |  |  | Chip Resistor; Thick Film; 1k; 50V; 0603; 100mW | 1K ±1% 0603 RoyalOhm
R20 | 25.4 | 87.63 | 270 | 0805 | 100K | Multicomp | MC01W08051100K | 9332405 |  |  | Chip Resistor; Thick Film; 100k; 150V; 0805; 100mW | 100K ±1% 0805 RoyalOhm
X1 | 76.07 | 92.46 | 90 | 3.2x1.5 | 32.768 | Epson | Q13FC13500004 | 1278036 |  |  | Crystal; 32.768kHz; 12.5pF; 3.2 x 1.5mm
Z1 | 10.29 | 89.41 | 0 | CT/CN0603 | CG0603MLC-05E | Bourns | CG0603MLC-05E | 1838966 | 652-CG0603MLC-05E |  | ESD Suppressor; 0603; 5 Volts
Z2 | 10.29 | 91.44 | 0 | CT/CN0603 | CG0603MLC-05E | Bourns | CG0603MLC-05E | 1838966 | 652-CG0603MLC-05E |  | ESD Suppressor; 0603; 5 Volts
Press-In Nuts for Iridium 9603N:
H1 | 16.27 | 16.50 |  |  | Press-In Nut | McMaster-Carr | 95117A411 |  |  | 95117A411 | Press-In Nut; 2-56
H2 | 41.27 | 16.50 |  |  | Press-In Nut | McMaster-Carr | 95117A411 |  |  | 95117A411 | Press-In Nut; 2-56
Non-surface mount components:
ANTENNA |  |  |  |  | SMA Jack | Johnson | 142-0711-821 | 1019328 |  |  | SMA End Launch Jack
BUZ |  |  |  |  | Buzzer | Pro Signal | ABI-003-RC | 1107581 |  |  | Buzzer 3V - 20VDC 15mA 95dB
BAT1 |  |  |  |  | PP3-Clip_Pair | Keystone | 593 + 594 | 723988 |  |  | Battery Contact, PP3 (9V), Snap Contact, Steel, Nickel Plated
BAT2 |  |  |  |  | PP3-Clip_Pair | Keystone | 593 + 594 | 723988 |  |  | Battery Contact, PP3 (9V), Snap Contact, Steel, Nickel Plated
RELAY1 |  |  |  |  | DPDT Latching | Omron | G6SK-2 3VDC |  | 653-G6SK-2DC3 |  | DPDT Latching Relay (Dual Coil) 3VDC
!RESET |  |  |  |  | Tactile Switch | Multicomp | MCDTS6-1N | 9471685 |  |  | Switch, SPST, 0.05A, 12VDC, 160gf
CLOSE_A |  |  |  |  | Tactile Switch | Multicomp | MCDTS6-1N | 9471685 |  |  | Switch, SPST, 0.05A, 12VDC, 160gf
CLOSE_B |  |  |  |  | Tactile Switch | Multicomp | MCDTS6-1N | 9471685 |  |  | Switch, SPST, 0.05A, 12VDC, 160gf
OPEN_A |  |  |  |  | Tactile Switch | Multicomp | MCDTS6-1N | 9471685 |  |  | Switch, SPST, 0.05A, 12VDC, 160gf
OPEN_B |  |  |  |  | Tactile Switch | Multicomp | MCDTS6-1N | 9471685 |  |  | Switch, SPST, 0.05A, 12VDC, 160gf
ON |  |  |  |  | Tactile Switch | Multicomp | MCDTS6-1N | 9471685 |  |  | Switch, SPST, 0.05A, 12VDC, 160gf
OFF |  |  |  |  | Tactile Switch | Multicomp | MCDTS6-1N | 9471685 |  |  | Switch, SPST, 0.05A, 12VDC, 160gf
DC-DC |  |  |  |  | DC-DC Converter | Recom | REC10-2405SRWZ/H3/A/M | 2846237 |  |  | Isolated DC-DC Converter, 10W, 5V, 2A, 24V Nominal Input
PI |  |  |  |  | https://shop.pimoroni.com/products/2x20-pin-gpio-header-for-raspberry-pi-2-b-a?variant=1132812269 |  |  |  |  |  | Female Header for Raspberry Pi GPIO pins
Iridium 9603N:
9603N |  |  |  |  |  | Iridium | 9603N |  |  |  | https://www.rock7.com/shop-product-detail?productId=50
Mounting hardware for Iridium 9603N:
SPACERS_x2 |  |  |  |  |  |  |  |  |  | 94669A100 | 4.5mm OD x 6mm Spacers for Iridium Module
SCREWS_x2 |  |  |  |  |  |  |  |  |  | 92185A081 | 2-56 x 7/16 Screws for Iridium Module
Cable for Iridium 9603N:
CABLE |  |  |  |  |  | Amphenol | A-1PA-132-025B2 | 2664624 |  |  | Amphenol AMC cable (u.FL compatible) 50ohm 25mm
SMA Antenna:
Iridium+GNSS |  |  |  |  |  | Maxtena | M1600HCT-P-SMA |  |  |  | Iridium + GNSS Passive Antenna with SMA connector

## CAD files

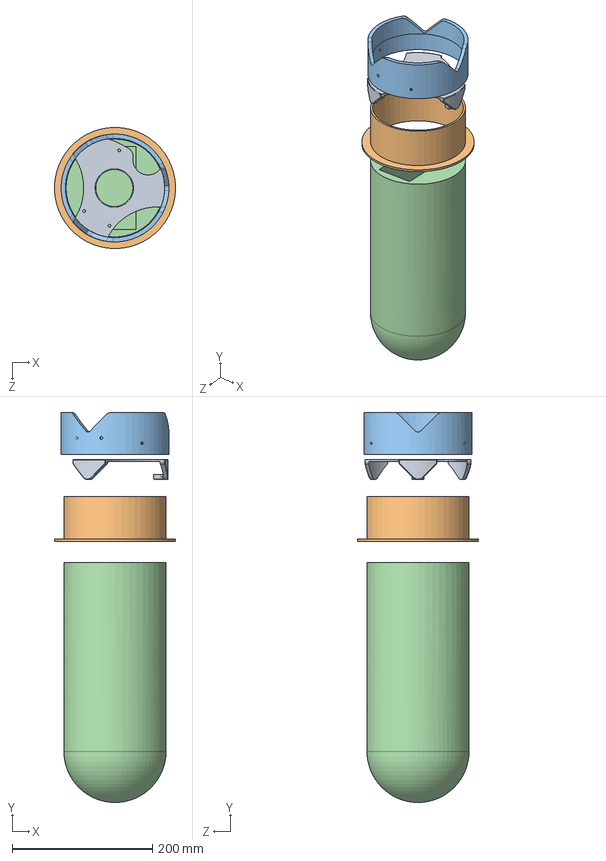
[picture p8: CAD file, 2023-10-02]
OpenSCAD/Crown/Inventor/SleeveModel_ASSEM.SLDASM
173.0 x 556.9 x 173.0 mm
ShortTube
Sleeve
Plate
Drop_Insulation

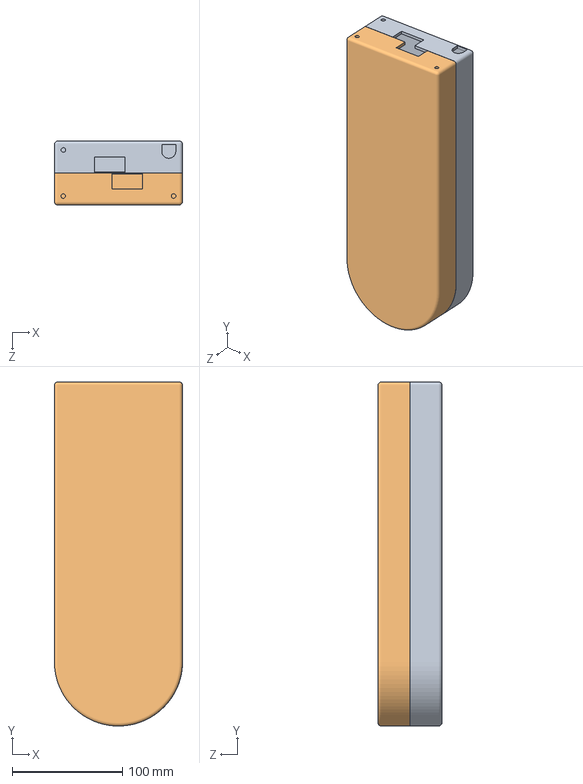
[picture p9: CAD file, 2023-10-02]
OpenSCAD/Crown/Inventor/ASSEM.SLDASM
116.3 x 312.1 x 58.0 mm
Case
Cover

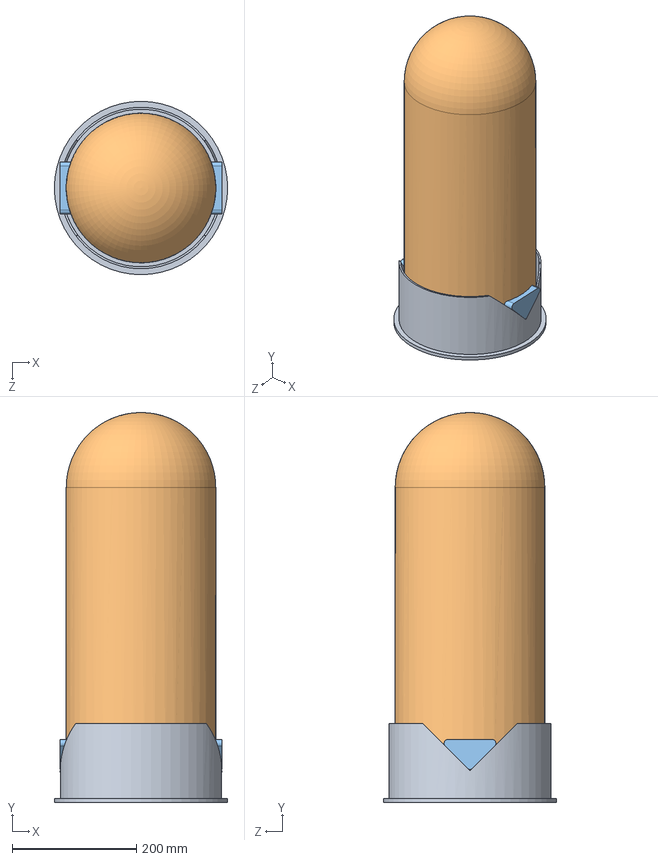
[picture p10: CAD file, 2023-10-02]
OpenSCAD/Crown/Inventor/Drop_ASSEM.SLDASM
279.4 x 628.7 x 279.4 mm
Tube
Drop_Insulation
Wedge x 2

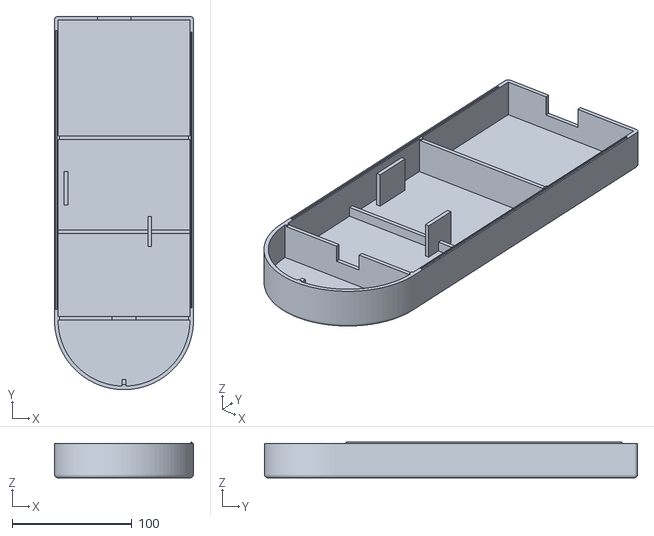
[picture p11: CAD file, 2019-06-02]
OpenSCAD/Case_2019_v1/Data_Recovery_System__Cover.stl
116.2 x 312.1 x 30.0

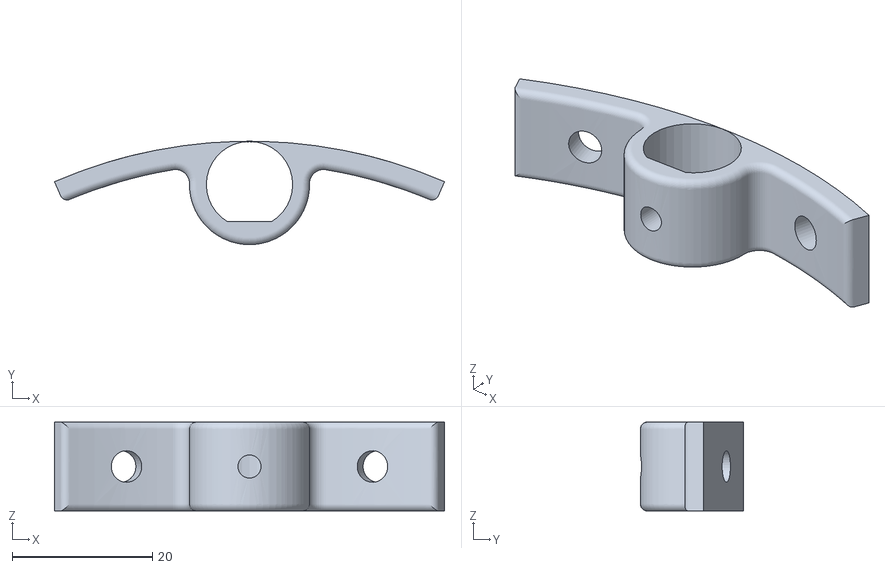
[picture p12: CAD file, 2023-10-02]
OpenSCAD/Crown/Data_Recovery_System__Cable_clip.STL
55.7 x 14.7 x 12.7

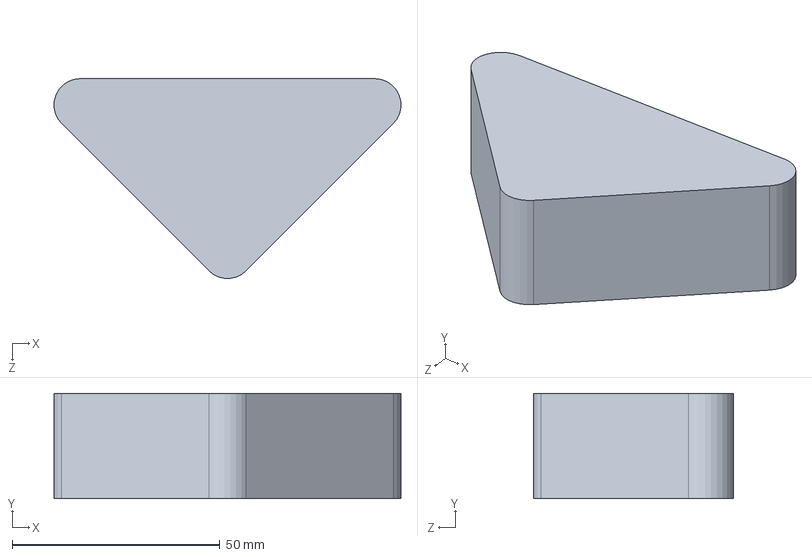
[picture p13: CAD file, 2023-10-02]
OpenSCAD/Crown/Inventor/Wedge.SLDPRT
83.6 x 25.4 x 48.1 mm

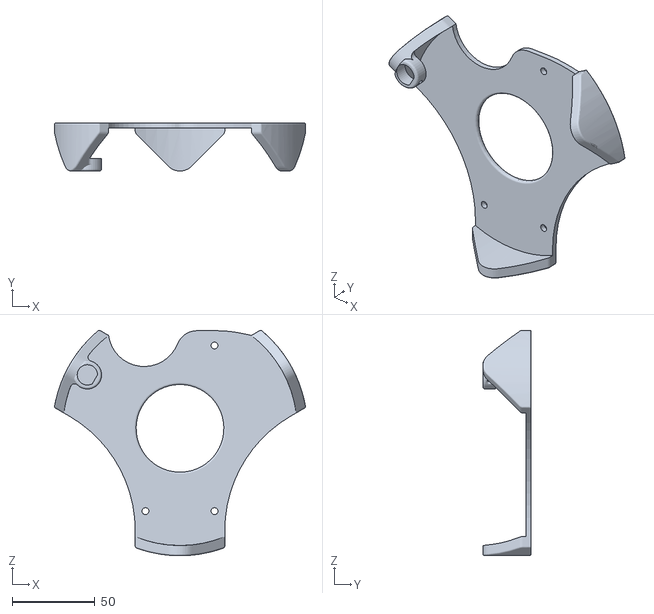
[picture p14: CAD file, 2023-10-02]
OpenSCAD/Crown/Data_Recovery_System__Crown.STL
151.8 x 29.0 x 136.3

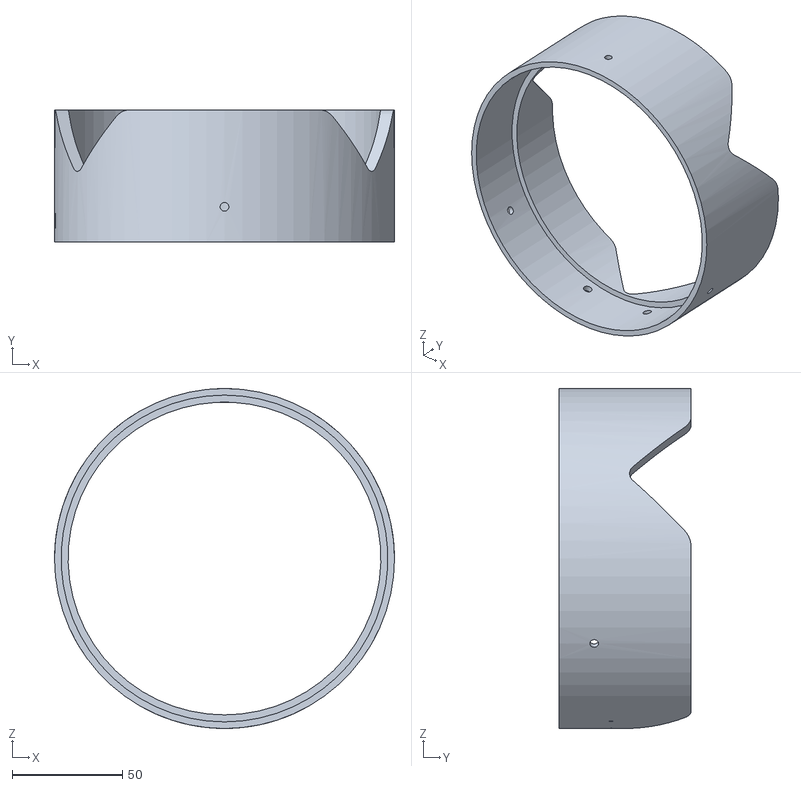
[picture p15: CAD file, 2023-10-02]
OpenSCAD/Crown/Data_Recovery_System__Mount.STL
154.1 x 60.0 x 154.1

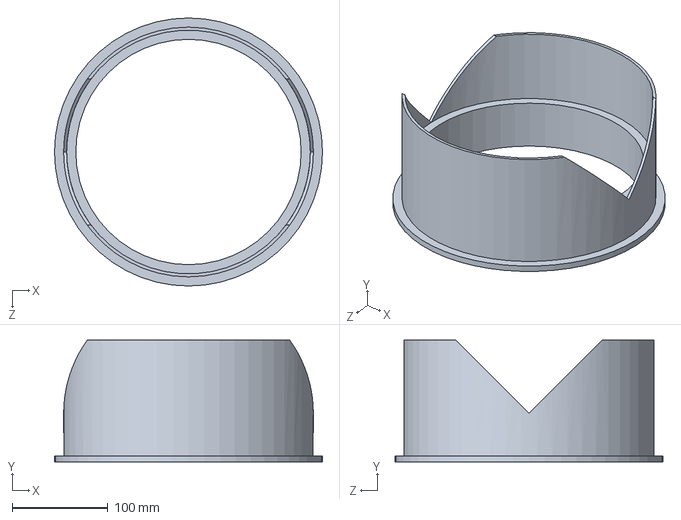
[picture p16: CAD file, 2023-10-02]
OpenSCAD/Crown/Inventor/Tube.SLDPRT
279.4 x 127.0 x 279.4 mm

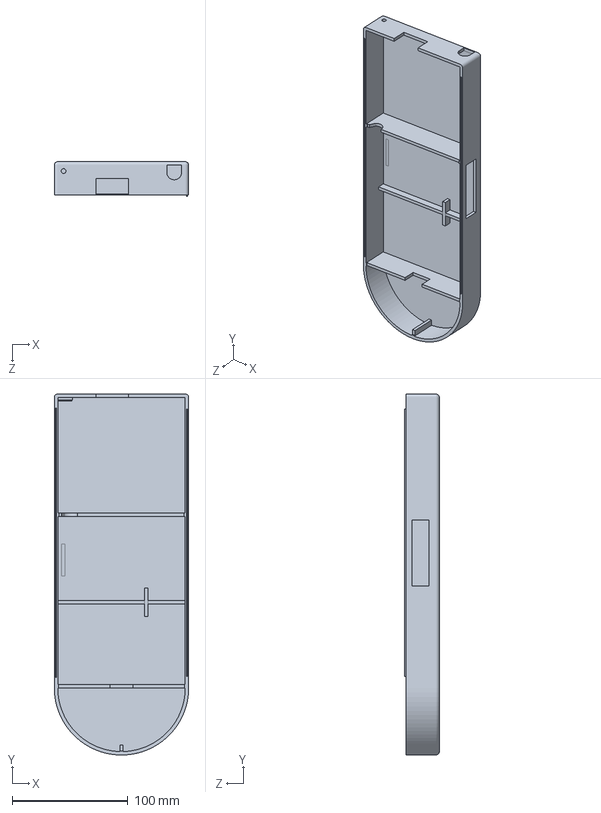
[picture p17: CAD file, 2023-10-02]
OpenSCAD/Crown/Inventor/DRS_COVER_V2.SLDPRT
116.2 x 312.1 x 30.0 mm

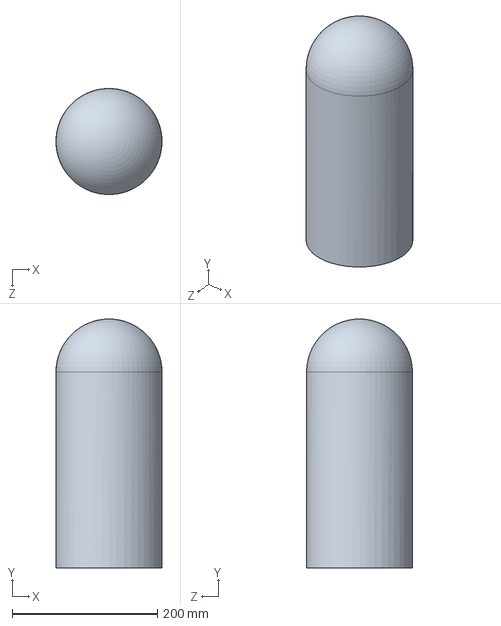
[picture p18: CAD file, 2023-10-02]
OpenSCAD/Crown/Inventor/Drop_Insulation.SLDPRT
146.1 x 342.9 x 146.1 mm

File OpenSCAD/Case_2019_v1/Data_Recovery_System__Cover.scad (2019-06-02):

// Cover for the Data Recovery System

$fn=90; // fragments

pcb_width = 108; // PCB width (X)
pcb_length = 305; // PCB length (Y)
pcb_thickness = 2.0; // PCB thickness (includes clearance)

module PCB()
{
    translate([0,0,(0-(pcb_thickness/2))])
        union()
        {
            cylinder(h=pcb_thickness, r=(pcb_width / 2));
            translate([(0-(pcb_width/2)),0,0])
                cube([pcb_width, (pcb_length - (pcb_width / 2)), pcb_thickness]);
        }
}

pi_height = 25.0; // Height of the Pi mounting screws above the PCB

USB = 1.1; // Width clearance for the USB connector

module void()
{
    translate([0,0,(0-wall)])
        union()
        {
            cylinder(h=(pi_height + (pcb_thickness/2) + wall), r=((pcb_width / 2) + USB));
            translate([(0-((pcb_width/2)+USB)),0,0])
                cube([(pcb_width + (2 * USB)), (pcb_length - (pcb_width / 2)), (pi_height + (pcb_thickness/2) + wall)]);
        }
}

wall = 3.0; // wall thickness

module floor()
{
    translate([(0-((pcb_width/2)+USB+(2*wall))),(0-((pcb_width / 2) + USB + (2 * wall))),(0-(2 * wall))])
        cube([(pcb_width + (2 * USB) + (4 * wall)), (pcb_length + USB + (4 * wall)), (2 * wall)]);
}

module shell()
{
    difference()
    {
        minkowski()
        {
            void();
            sphere(r=wall);
        }
        floor();
        void();
    }
}

cross_wall_y = 205; // Y position of cross wall

module cross_wall()
{
    wall_width = (pcb_width + (2 * USB) + wall);
    translate([(0-(wall_width / 2)),(cross_wall_y - (pcb_width / 2)), 0])
        cube([wall_width, wall, (pi_height + (wall / 2) + (pcb_thickness / 2))]);
}

battery_wall_y = 128; // Y position of cross wall above battery
battery_height = 18; // Z height of the battery above the PCB surface
battery_tab_length = 25; // Y length of battery tab
battery_tab_offset = 20; // X offset of right side of battery tab

module battery_wall()
{
    wall_width = (pcb_width + (2 * USB) + wall);
    translate([(0-(wall_width / 2)),(battery_wall_y - ((pcb_width / 2) + (wall/2))), (battery_height + (pcb_thickness / 2))])
        cube([wall_width, wall, (pi_height + (wall / 2) - battery_height)]);
}

module battery_tab()
{
    translate([(0-(battery_tab_offset + wall)),(battery_wall_y - ((pcb_width / 2) + (battery_tab_length/2))), 0])
        cube([wall, battery_tab_length, (pi_height + (wall / 2) + (pcb_thickness / 2))]);    
}

antenna_width = 20; // X width of antenna slot
antenna_height = 12; // Z height of antenna slot above PCB (worst case)

module antenna_wall()
{
    wall_width = (pcb_width + (2 * USB) + wall);
    difference()
    {
        translate([(0-(wall_width / 2)), 0, 0])
            cube([wall_width, wall, (pi_height + (wall / 2) + (pcb_thickness / 2))]);
        translate([(0-(antenna_width / 2)), (0-(wall/2)), 0])
            cube([antenna_width, (2*wall), (antenna_height + (pcb_thickness / 2))]);
    }
}

pi_usb_wall_y = 164.5; // Y position of the Pi USB retaining wall
pi_usb_wall_offset = 47; // X offset of the left side of the USB retaining wall
pi_usb_wall_length = 28; // Y length of the USB retaining wall

module pi_usb_wall()
{
    translate([pi_usb_wall_offset,(pi_usb_wall_y - ((pcb_width / 2) + (pi_usb_wall_length/2))), 0])
        cube([wall, pi_usb_wall_length, (pi_height + (wall / 2) + (pcb_thickness / 2))]);    
}

shark_width = 28; // X width of the shark opening
shark_offset = 6; // X offset of the shark opening
shark_height = 13.5; // Z height of the shark opening above the PCB

module shark()
{
    translate([(0-shark_offset),(pcb_length - ((pcb_width/2) + (wall/2))), (0-(pcb_thickness / 2))])
        cube([shark_width, (2 * wall), (shark_height + pcb_thickness)]);    
}

module nose()
{
    translate([(0-(wall/2)),(0-((pcb_width/2) + USB + (wall/2))), 0])
        cube([wall, ((2 * wall) + USB), (pi_height + (wall / 2) + (pcb_thickness / 2))]);    
}

tab_width = 0.8; // tab X width
tab_reduce = 10; // start and end the tab this far from the end of each straight edge
tab_height = 1; // tab Z height
slot_gap_x = 0.2; // total X slot clearance
slot_gap_y = 2; // total Y slot clearance
slot_gap_z = 0.5; // Z slot clearance

module tab()
{
    translate([(0-((pcb_width/2) + USB + tab_width + ((wall-tab_width)/2))), tab_reduce, (0 - tab_height)])
        cube([tab_width, (pcb_length - ((pcb_width / 2) + (2 * tab_reduce))), (2 * tab_height)]);    
}

module slot()
{
    slot_width = tab_width + slot_gap_x;
    translate([((pcb_width/2) + USB + ((wall-slot_width)/2)), (tab_reduce - (slot_gap_y / 2)), (0 - (tab_height + slot_gap_z))])
        cube([slot_width, (pcb_length  + slot_gap_y - ((pcb_width / 2) + (2 * tab_reduce))), (2 * (tab_height + slot_gap_z))]);    
}

module finished_shell()
{
    difference()
    {
        union()
        {
            shell();
            cross_wall();
            battery_wall();
            battery_tab();
            antenna_wall();
            pi_usb_wall();
            nose();
            tab();
        }
        PCB();
        shark();
        slot();
    }
}

module flipped_shell()
{
    translate([0,0,((pcb_thickness/2)+pi_height+wall)])
        rotate(a=[0,180,0])
            finished_shell();
}

flipped_shell();

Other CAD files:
OpenSCAD/Case_2023_v8/Data_Recovery_System__Cover_Side1.stl
OpenSCAD/Heatsink/Data_Recovery_System__Heatsink.dwg
OpenSCAD/Case_2023_v8/Data_Recovery_System__Cover_Side2.stl
OpenSCAD/Crown/Inventor/Cover.SLDPRT
OpenSCAD/Crown/Inventor/DRS_BASE_V2.SLDPRT
OpenSCAD/Crown/Inventor/Sleeve.SLDPRT
OpenSCAD/Crown/Inventor/Plate.SLDPRT
OpenSCAD/Case_2023_v8/Data_Recovery_System__Cover_Side2.scad
OpenSCAD/Crown/Drawings/SleeveModel_ASSEM.SLDDRW
OpenSCAD/Crown/Inventor/CableMount.SLDPRT
OpenSCAD/Crown/Inventor/Case.SLDPRT
OpenSCAD/Crown/Inventor/Case.stl
OpenSCAD/Crown/Inventor/Connector_Sheath.SLDPRT
OpenSCAD/Crown/Inventor/Cover.stl
OpenSCAD/Crown/Inventor/ShortTube.SLDPRT
OpenSCAD/Heatsink/Data_Recovery_System__Heatsink.ipt

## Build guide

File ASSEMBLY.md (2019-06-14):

# ASSEMBLY

This guide contains instructions on how to assemble and configure the DRS.

If your DRS has been assembled previously and you only want to make it ready for flight, the please skip forward to [Step 8](https://github.com/PaulZC/Data_Recovery_System/blob/master/ASSEMBLY.md#step-8-attach-the-tether-and-parachute).

## Prerequisites

- The DRS PCB should have been prepared and tested following the instructions in [PCB.md](https://github.com/PaulZC/Data_Recovery_System/blob/master/PCB.md)
- The Raspberry Pi should have been configured and have the [DRS_Python_Tools](https://github.com/PaulZC/DRS_Python_Tools) installed following the instructions in [PI.md](https://github.com/PaulZC/Data_Recovery_System/blob/master/PI.md)
- The two HiTec servos should have been prepared following the instructions in [SERVO.md](https://github.com/PaulZC/Balloon_Cut-Down_Device/blob/master/SERVO.md)
- The two archery release aids should have been prepared following the instructions in [SHARK.md](https://github.com/PaulZC/Balloon_Cut-Down_Device/blob/master/SHARK.md)

## Step 1: Install the Raspberry Pi on the underside of the DRS PCB

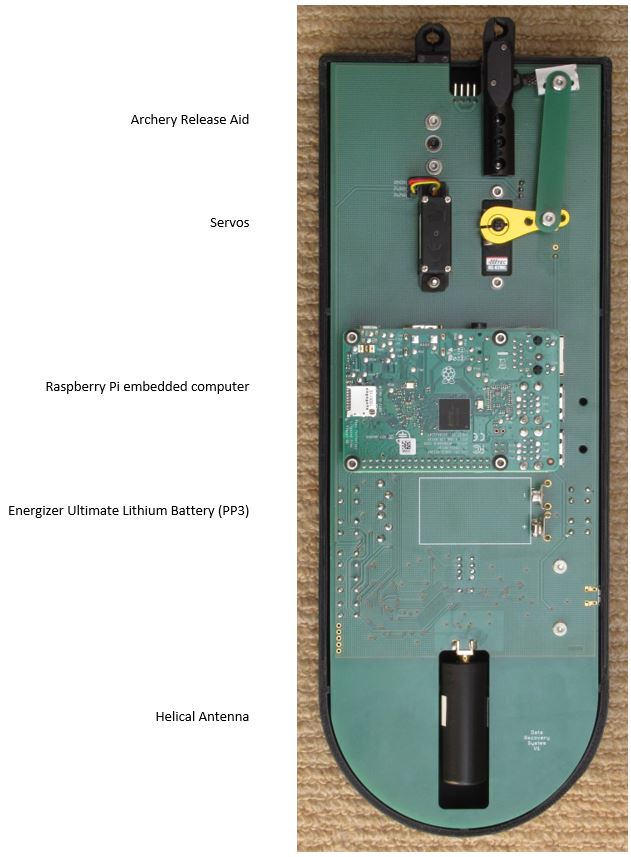
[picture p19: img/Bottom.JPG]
Bottom


- Push an [11mm 2x20 Header](https://shop.pimoroni.com/products/2x20-pin-gpio-header-for-raspberry-pi-2-b-a?variant=1132812269) on the Raspberry Pi's GPIO pins
- The header pins are just long enough to reach the PCB when the Pi is mounted
- Apply a liberal coating of [Acrylic Protective Lacquer (conformal coating)](https://uk.rs-online.com/web/p/conformal-coatings/3217324/) to both sides of the Raspberry Pi PCB, covering all components except the connectors
- Once the coating is dry, mount the Pi on the underside of the PCB using:
  - Four 30mm M2.5 stainless steel screws [McMaster part 91292a037](https://www.mcmaster.com/91292a037)
  - Four 19mm aluminium spacers [McMaster part 94669a112](https://www.mcmaster.com/94669a112)
  - Sixteen M2.5 fiber washers [McMaster part 95225a310](https://www.mcmaster.com/95225a310)
  - Four M2.5 Nylock nuts [McMaster part 93625a102](https://www.mcmaster.com/93625a102)
- Solder all 40 header pins to the PCB

## Step 2: Mount the two archery releases on the PCB

- Use six 1/4" 4-40 UNC screws [McMaster part 92196a106](https://www.mcmaster.com/92196a106)
- Apply threadlock to each screw first
- Release A (for the tether) goes on the underside of the PCB, release B (for the parachute) goes on top

## Step 3: Mount the two servos on the PCB

- Press the supplied rubber inserts into the holes on the sides of the servos
- Insert the brass inserts into the bottom of each rubber insert
- Mount the servos using:
  - Four 14mm M2.5 stainless steel screws [McMaster part 91292a017](https://www.mcmaster.com/91292a017)
  - Four M2.5 Nylock nuts [McMaster part 93625a102](https://www.mcmaster.com/93625a102)
  - Four M2.5 stainless steel washers [McMaster part 90965a115](https://www.mcmaster.com/90965a115)
- Place the washers under the screw heads
- The Nylock nuts will tighten against the flat face on the end of each brass insert
- Do not install the servo arms yet
- Servo A goes on the underside of the PCB, servo B goes on top

## Step 4: Upload the Arduino code

- After following the instructions in [PCB.md](https://github.com/PaulZC/Data_Recovery_System/blob/master/PCB.md) the SAMD microcontroller will have been configured with its bootloader and the PCB components will have been tested using the Arduino code in the [Test folder](https://github.com/PaulZC/Data_Recovery_System/tree/master/Arduino/Data_Recovery_System_V1_Test)
- The next step is to upload the DRS Arduino code to the microcontroller
- Open the Arduino IDE and connect the DRS to your computer using a micro-USB cable
- Check the Tools\Board and Tools\Port settings. The DRS should appear as an "Adafruit Feather M0"

Board

- Download and open [Data_Recovery_System_V1.ino](https://github.com/PaulZC/Data_Recovery_System/tree/master/Arduino/Data_Recovery_System_V1) in the IDE
- Click on the arrow icon below the Edit menu. This will compile the code and upload it onto the DRS
- As soon as the upload is finished, click on the Tools menu and then "Serial Monitor"
- Change the baud rate to 115200 using the pull-down menu at the bottom of the serial monitor window
- All being well, after 10 seconds you should see messages saying:

Serial_Monitor

## Step 5: Configure the servo positions

The open and closed servo positions for DRS1-5 are included in the Arduino code. Only follow this procedure if the positions need to be modified (e.g. after removing the arm from a servo) or you are using a new PCB

The servos cannot be moved unless: at least one 9V battery has been installed; the latching relay is 'ON'.

The servos are powered by a 5V regulator which is powered by the 9V batteries.

The 'ON' and 'OFF' buttons, which control the state of the latching relay, are only operational when the Raspberry Pi is powered up. They draw 3.3V power from the Pi (not the microcontroller).

- Connect 24V DC power to the power connector. If connecting to the 4-pin header: the two outer pins are 0V; the two inner pins are 24V
- The Pi will boot up and attempt to connect to WiFi
- If WiFi is not available, you can connect a laptop to the Pi using the Ethernet port. The Pi acts as a DHCP server (see steps 25-29 in [PI.md](https://github.com/PaulZC/Data_Recovery_System/blob/master/PI.md))
- Clip a 9V battery into one set of battery clips (only one battery is required, not two)
- Press the ON button to enable power for the servos
- To place the DRS into 'Set Servo A' mode:
  - Push and hold down the OPEN_A and CLOSE_A switches
  - Push and release the RESET switch
  - Wait until the NeoPixel has gone cyan before releasing the OPEN_A and CLOSE_A switches
- The servo will move to its mid-range position
- You can now install the servo arm. Orient the arm at four o' clock (with the PCB oriented as in the above photo)
- Use a 4mm M3 low profile shoulder screw ([McMaster part 90323a211](https://www.mcmaster.com/90323a211)) to fix the servo linkage to the archery release trigger block
- Do not connect the linkage to the servo arm yet
- Push the archery release trigger so that the release jaws are closed
- Pressing the CLOSE_B switch will step the servo arm towards the archery release aid. Pressing OPEN_B will step it away. Push and hold for larger movements
- Move the arm until it is positioned as shown:

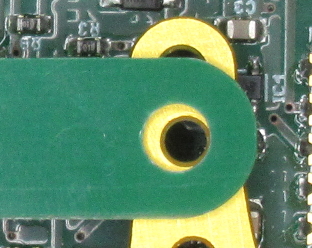
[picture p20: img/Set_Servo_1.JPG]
Set_Servo_1


- Press the CLOSE_A switch to store the position in flash memory. The NeoPixel will flash green as the write takes place
- Pull the archery release trigger so that the release jaws are open
- Move the servo arm using OPEN_B and CLOSE_B until it is positioned as shown:

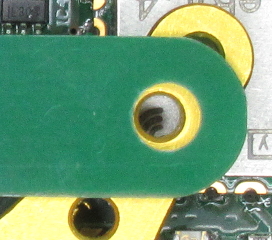
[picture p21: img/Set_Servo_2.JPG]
Set_Servo_2


- Press the OPEN_A switch to store the position in flash memory. The NeoPixel will flash green as the write takes place
- Press the RESET switch to leave 'Set Servo A' mode
- You can now secure the trigger linkage to the servo arm using another shoulder screw
- Repeat for servo B
  - Push and hold down the OPEN_B and CLOSE_B switches
  - Push and release the RESET switch
  - Release the OPEN_B and CLOSE_B switches after the NeoPixel has gone cyan
  - Use the OPEN_A and CLOSE_A switches to move the servo
  - Use the OPEN_B and CLOSE_B switches to store the servo positions
  - Press RESET when done

The serial monitor messages will list the new servo positions. You should copy these values into the Arduino code and re-upload to the DRS when convenient.

## Step 6: Test the servos

The servos can be tested using the serial monitor. Make sure the Baud rate is set to 115200 and the line ending is set to Newline.

The serial monitor will display the NMEA messages from the MAX-M8Q GNSS receiver.

- Type OPEN_A into the text box at the top of the serial monitor and either click 'Send' or press enter
- Servo A will move to the open position
- CLOSE_A will move servo A to the closed position
- Likewise OPEN_B and CLOSE_B can be used to move servo B
- These commands are only actioned if received through the serial monitor. They are ignored if sent via the Raspberry Pi's serial port

## Step 7: Other serial monitor commands

The Arduino code will also respond to the following commands if they are submitted from the serial monitor through the micro-USB port:
- SOUNDER_ON will enable sounder beeps every 5 seconds
- SOUNDER_OFF will disable sounder beeps
- GoGoGo will cause the microcontroller to go into 'Gone' (Drop) mode: servo A will be opened, Iridium messages will be set every 2 minutes

'Gone' mode can only be disabled by:
- Pressing and holding OPEN_A, CLOSE_A, OPEN_B and CLOSE_B
- Pressing and releasing RESET
- Keeping OPEN_A, CLOSE_A, OPEN_B and CLOSE_B held down until the NeoPixel goes green

The Raspberry Pi's serial port cannot be used to move the servos or enable/disable the sounder. GoGoGo is the only valid command that can be sent by the Pi.

## Step 8: Attach the tether and parachute

It is not good practice to move the servos by hand. They can be damaged by being back-driven.
So, the best way to close the servos when attaching the tether and parachute is using the serial monitor commands described above.

The tether is a length of [Size 4N nylon cord (2.4mm diameter)](https://www.ropesdirect.co.uk/4n-nylon-cord-132m.html).
Cut a ~0.75m length and seal the ends with flame to prevent fraying. Close the jaws of Servo A mid-way along the tether.

The Rocketman 4' parachute has a stitched loop at the center point of the suspension lines. Close the jaws of servo B around the loop as shown below:

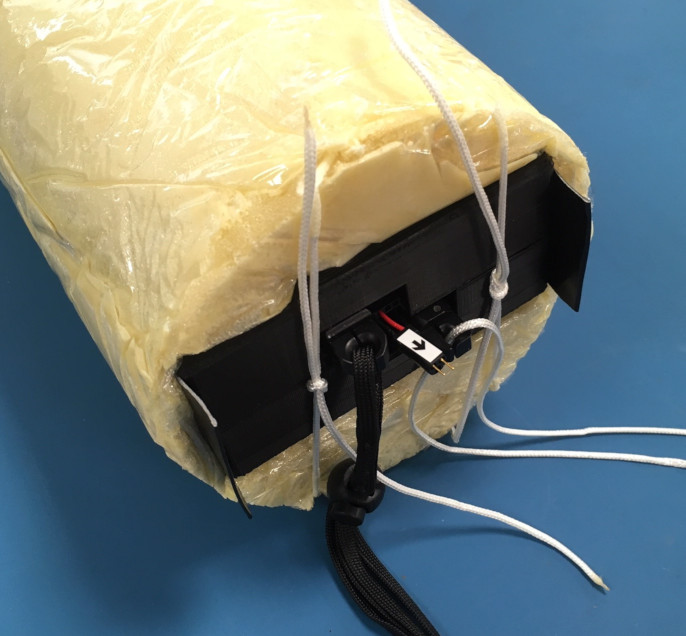
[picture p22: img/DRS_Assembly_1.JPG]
DRS_Assembly_1


## Step 9: Power down and connect the batteries

Before powering down the DRS, so you can finish the assembly, please check:
  - That the microcontroller has been reset to 'Waiting for Go' mode if required
  - Both archery releases are closed and the tether and parachute are attached

- Reset the Omron relay by pressing the OFF button. This disconnects the 9V batteries. The microcontroller will stay on as it is drawing power from the micro-USB cable
- Turn off the microcontroller by unplugging the micro-USB cable
- Shutdown the Pi over WiFi or Ethernet with: sudo shutdown now
- Wait for the green LED on the Pi to stop blinking
- Disconnect the 24V power to the Pi
- Install the low extraction force power connector plug if required

## Step 10: Insert the batteries

- Insert two fresh Energizer Ultimate Lithium 9V PP3 (L522) into the battery clips, securing them with hot glue or double-sided adhesive tape

## Step 11: Close up the case

- The 3D printed case is made from two identical parts which clip together with a simple tongue and groove joint
- Apply a thin layer of silicone sealant across the 'wall' pieces in each half of the case that divide the servos and releases from the Raspberry Pi
- Place the PCB into the bottom half of the case
- Position the top half and press together to engage the tongue and groove joint
- Tape the two halves of the case together using a long length of duct tape. Ensure that the ends of the tape are folded over into tabs. These will be useful when pulling the case out of the foam enclosure (it is a tight fit!)

DRS_Assembly_1

## Step 12: Insert the case into the foam enclosure

- Push the case into the foam enclosure
- Securely knot the nylon cord which runs through the foam around the end of the case. Trim and seal the cord ends with flame

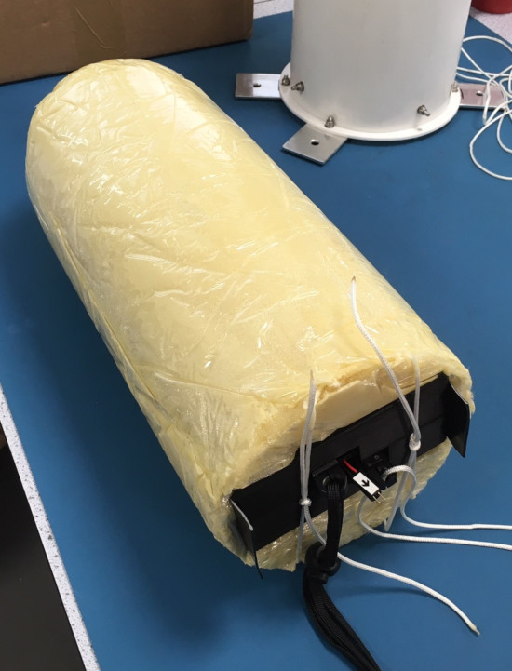
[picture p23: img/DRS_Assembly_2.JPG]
DRS_Assembly_2


- Attach the low extraction force power connector socket cable. Ensure the arrows are aligned
- Secure nylon line to the power cable approx. 100mm from the connector. You might find it useful to tie a single knot in the power cable and feed the tie-wrap through that

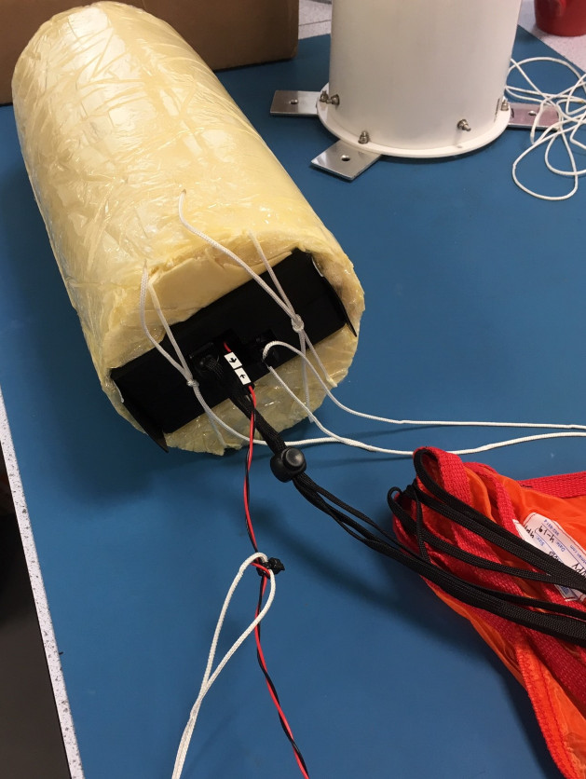
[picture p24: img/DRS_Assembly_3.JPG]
DRS_Assembly_3


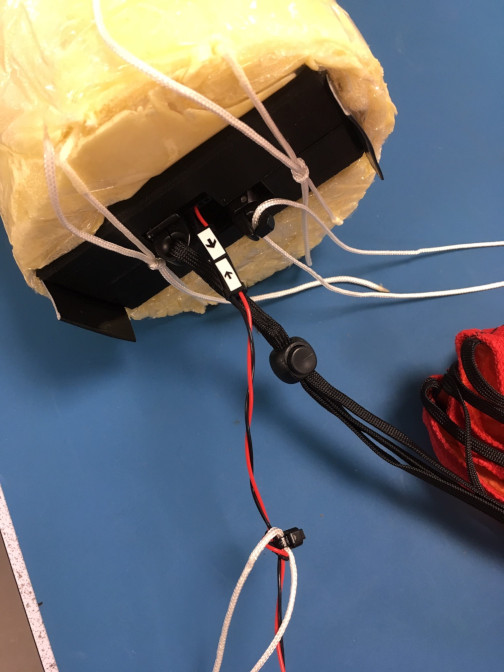
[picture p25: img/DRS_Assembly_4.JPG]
DRS_Assembly_4


## Step 13: Fold the parachute

Fold the parachute following the instructions on the [Rocketman website](https://the-rocketman.com/packing/)

Our method follows the 'dog barf' method - but without the 'dog barf' (cellulose insulation) itself

## Step 14: Insert into the launch tube

The launch tube is made from:
- 350mm of 150mm [ventilation ducting](https://www.amazon.co.uk/Blauberg-UK-150-Extractor-Ventilation/dp/B06XDG47JB/ref=sr_1_8)
- a 150mm [pipe spigot](https://www.amazon.co.uk/Spigot-Flange-Mounting-Ventilation-Connection/dp/B01KABZEJU/ref=sr_1_15)
- two aluminium brackets (one bent so it fits under the other)
- secured together with eight M4 stainless steel button head screws, sixteen washers and eight Nylock nuts

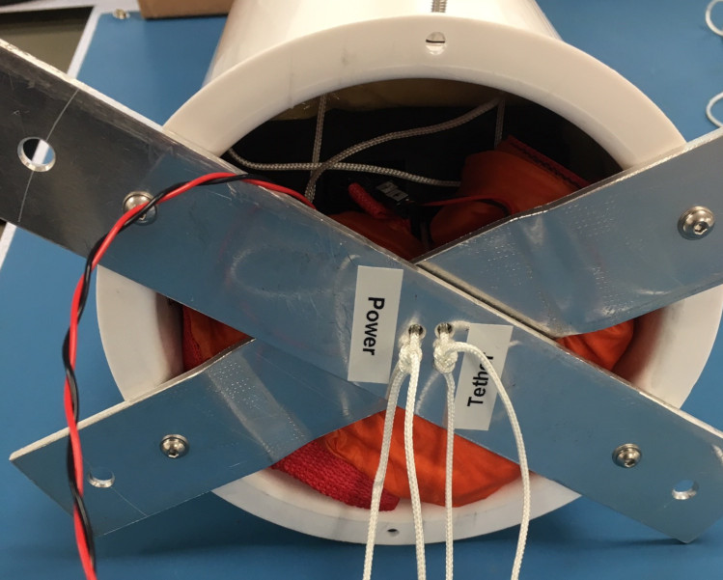
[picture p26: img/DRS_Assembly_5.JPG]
DRS_Assembly_5


- Pass the tether and power cords through the pairs of holes in the aluminium brackets
- Hold the parachute against the bottom of the foam enclosure while drawing the cords through the brackets
- Once fully inserted, the parachute should be compressed over to one side of the tube and trapped by the tether. This should leave the power connector available for inspection

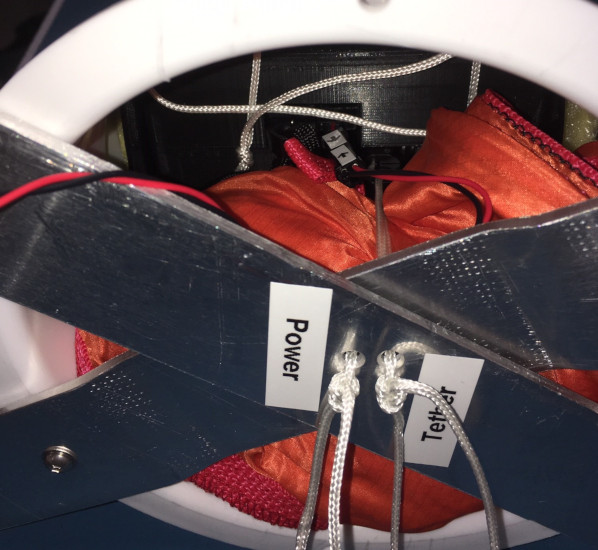
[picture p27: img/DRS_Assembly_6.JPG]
DRS_Assembly_6


- Securely knot the tether and power cords. Cut the cord short and seal the ends with flame
- The DRS is ready to be secured to the gondola

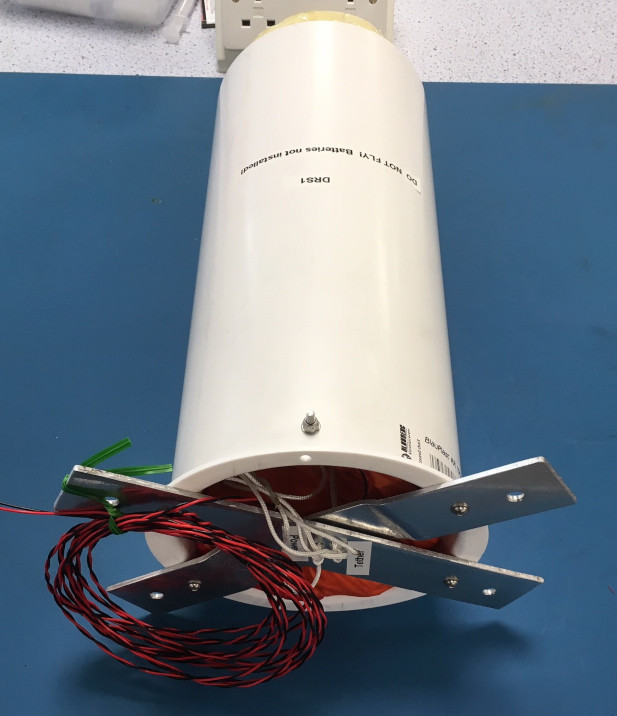
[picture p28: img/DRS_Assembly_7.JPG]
DRS_Assembly_7


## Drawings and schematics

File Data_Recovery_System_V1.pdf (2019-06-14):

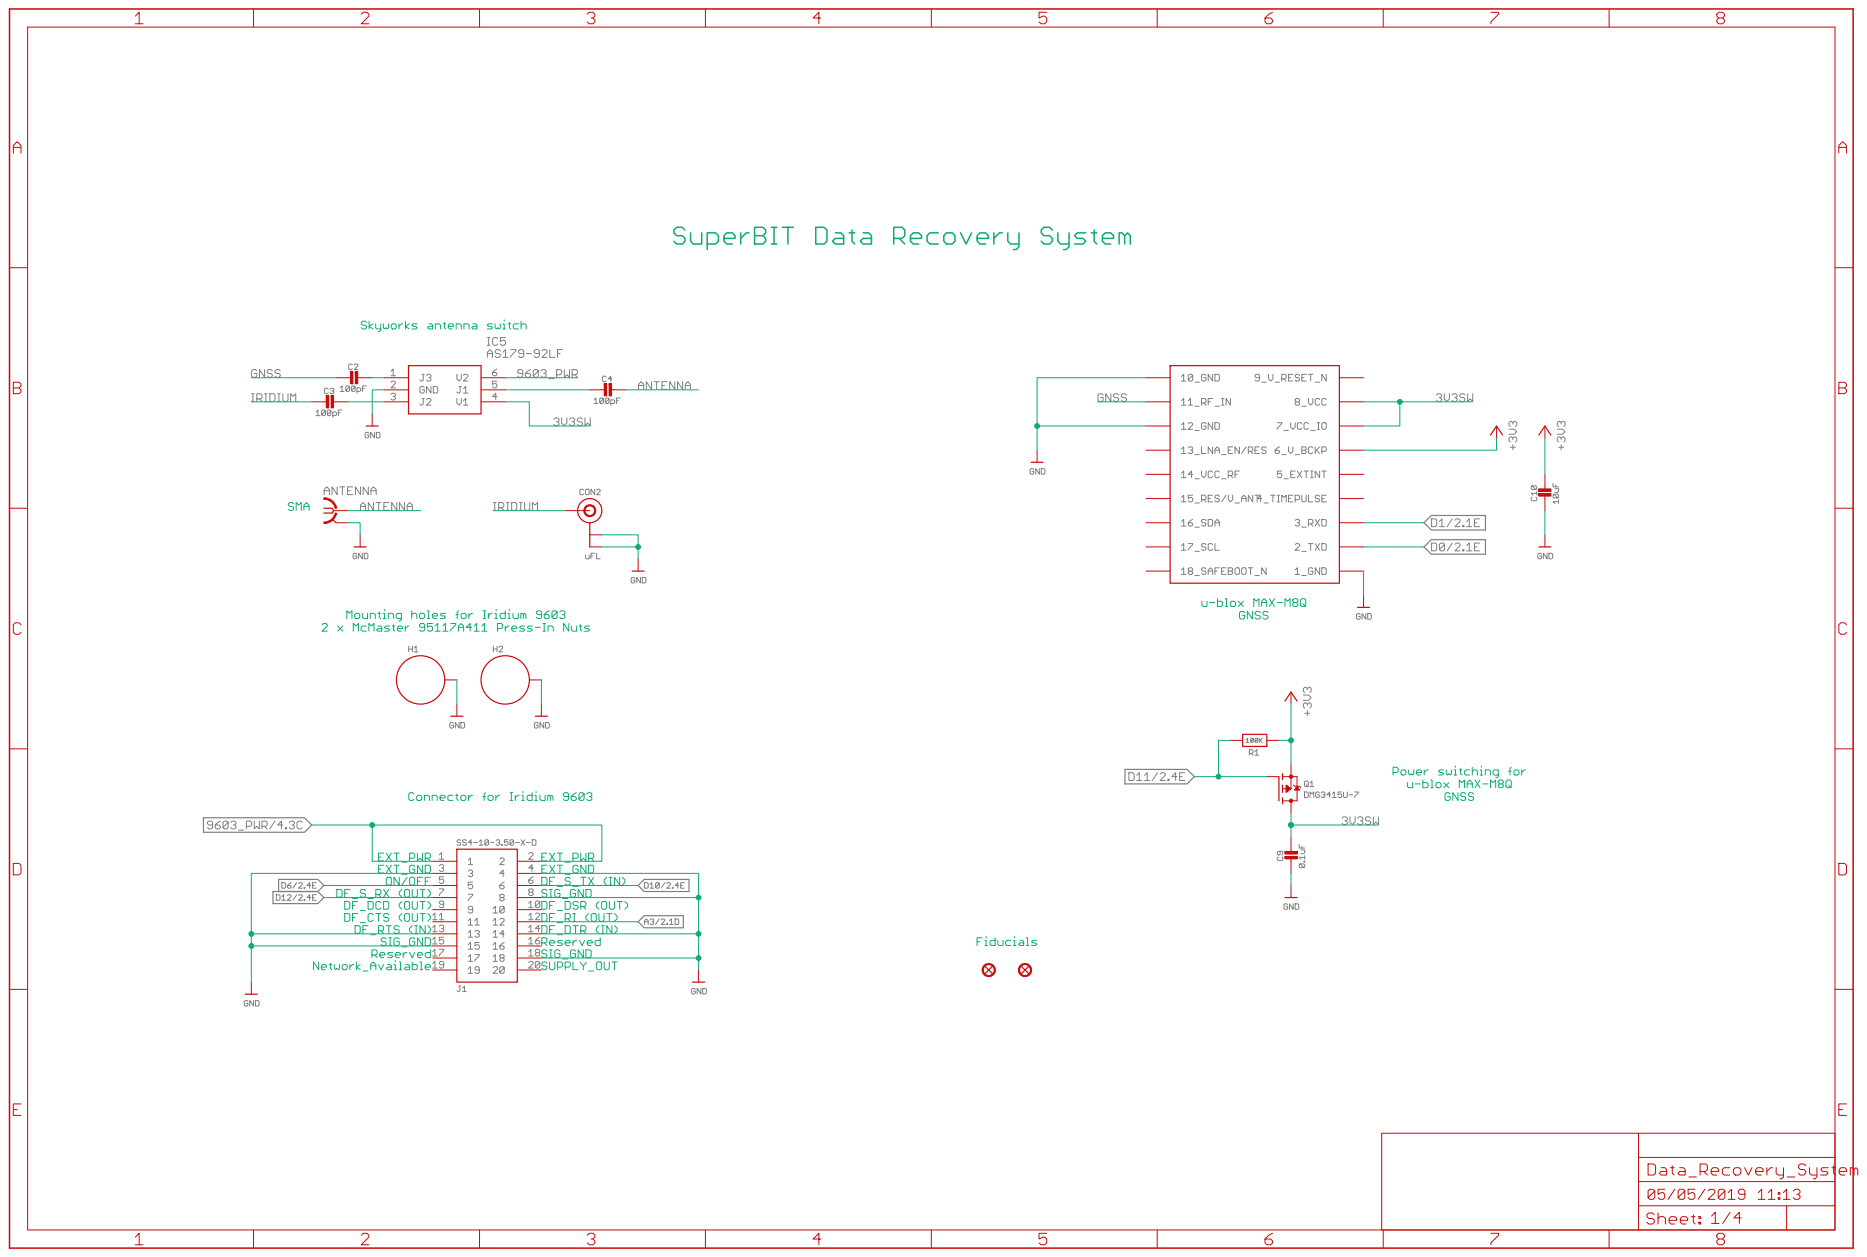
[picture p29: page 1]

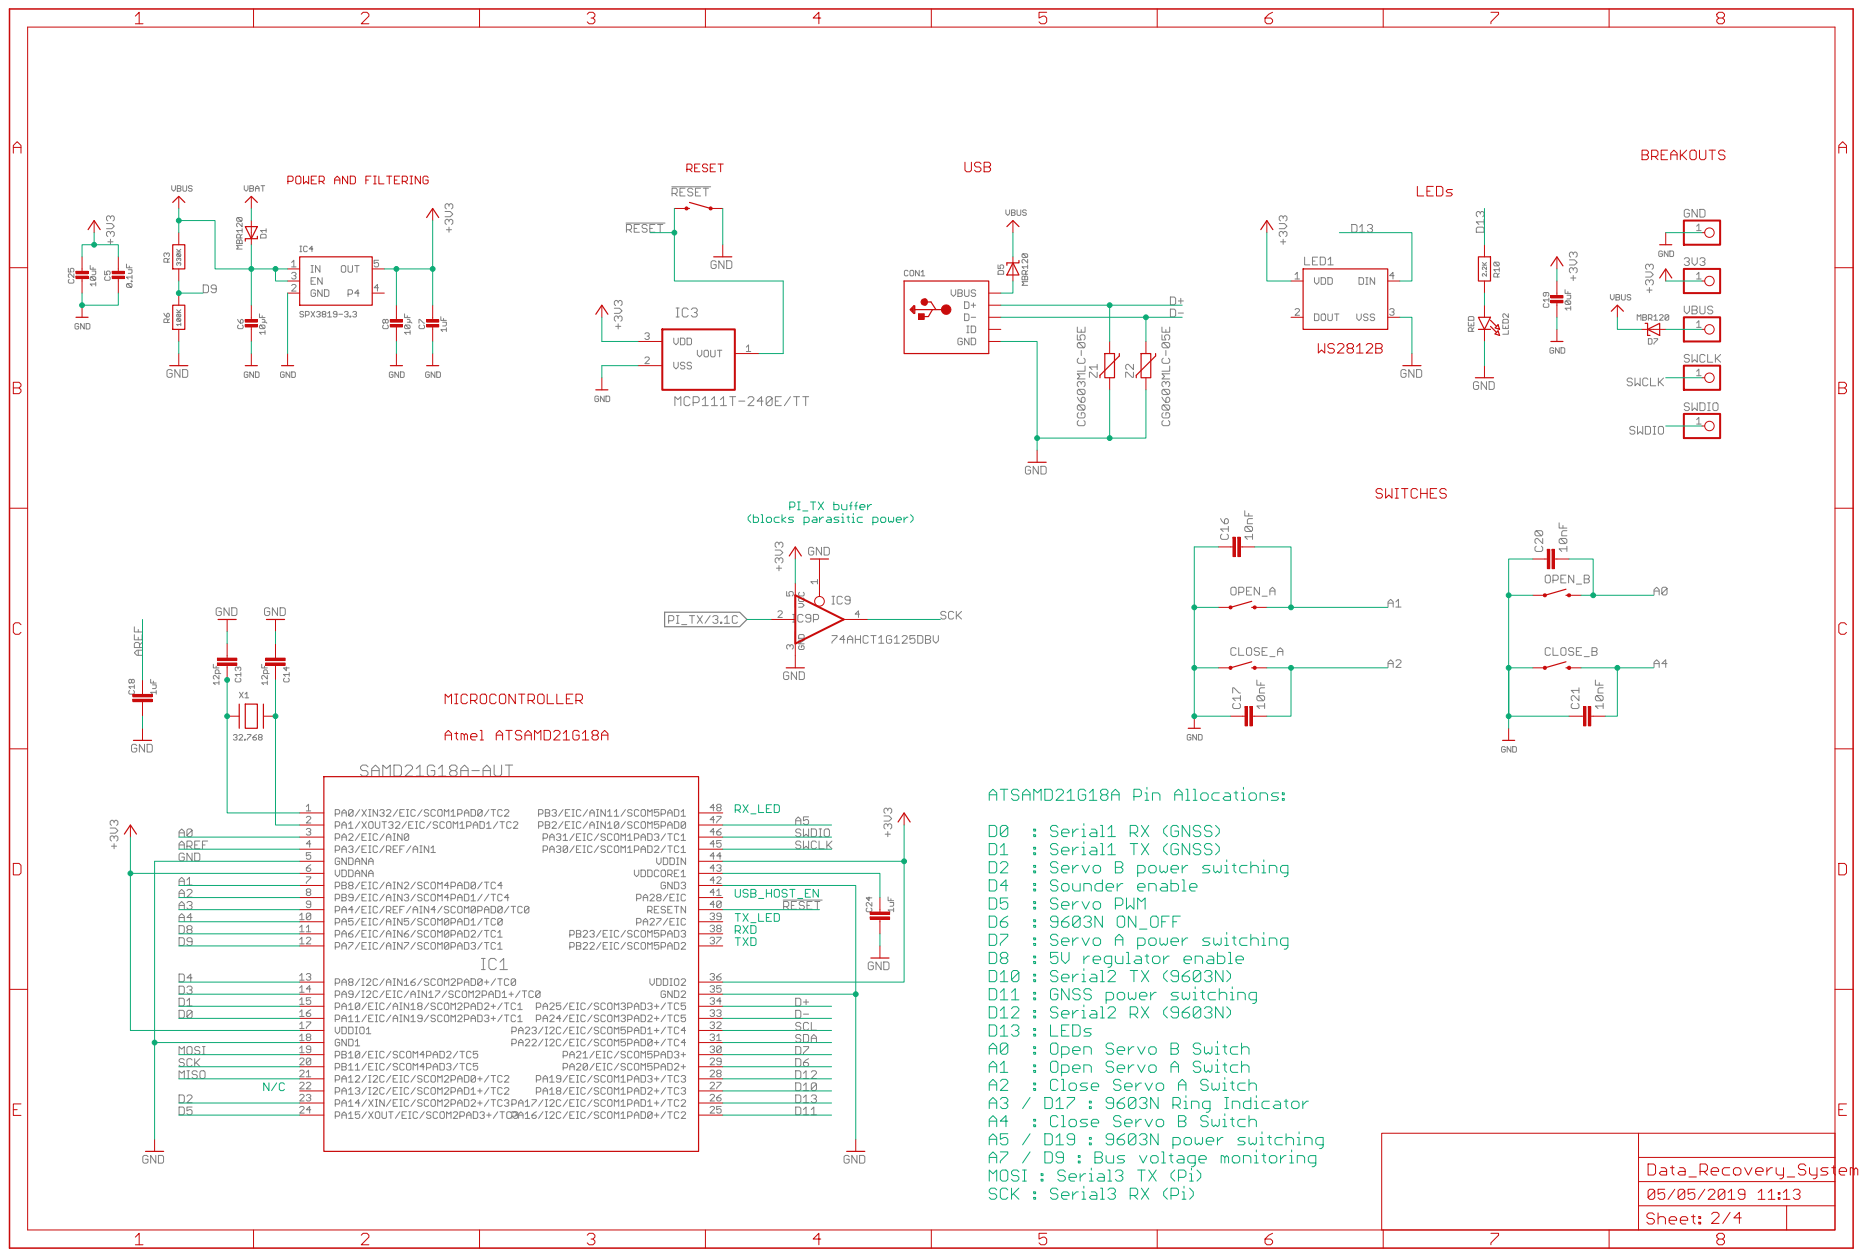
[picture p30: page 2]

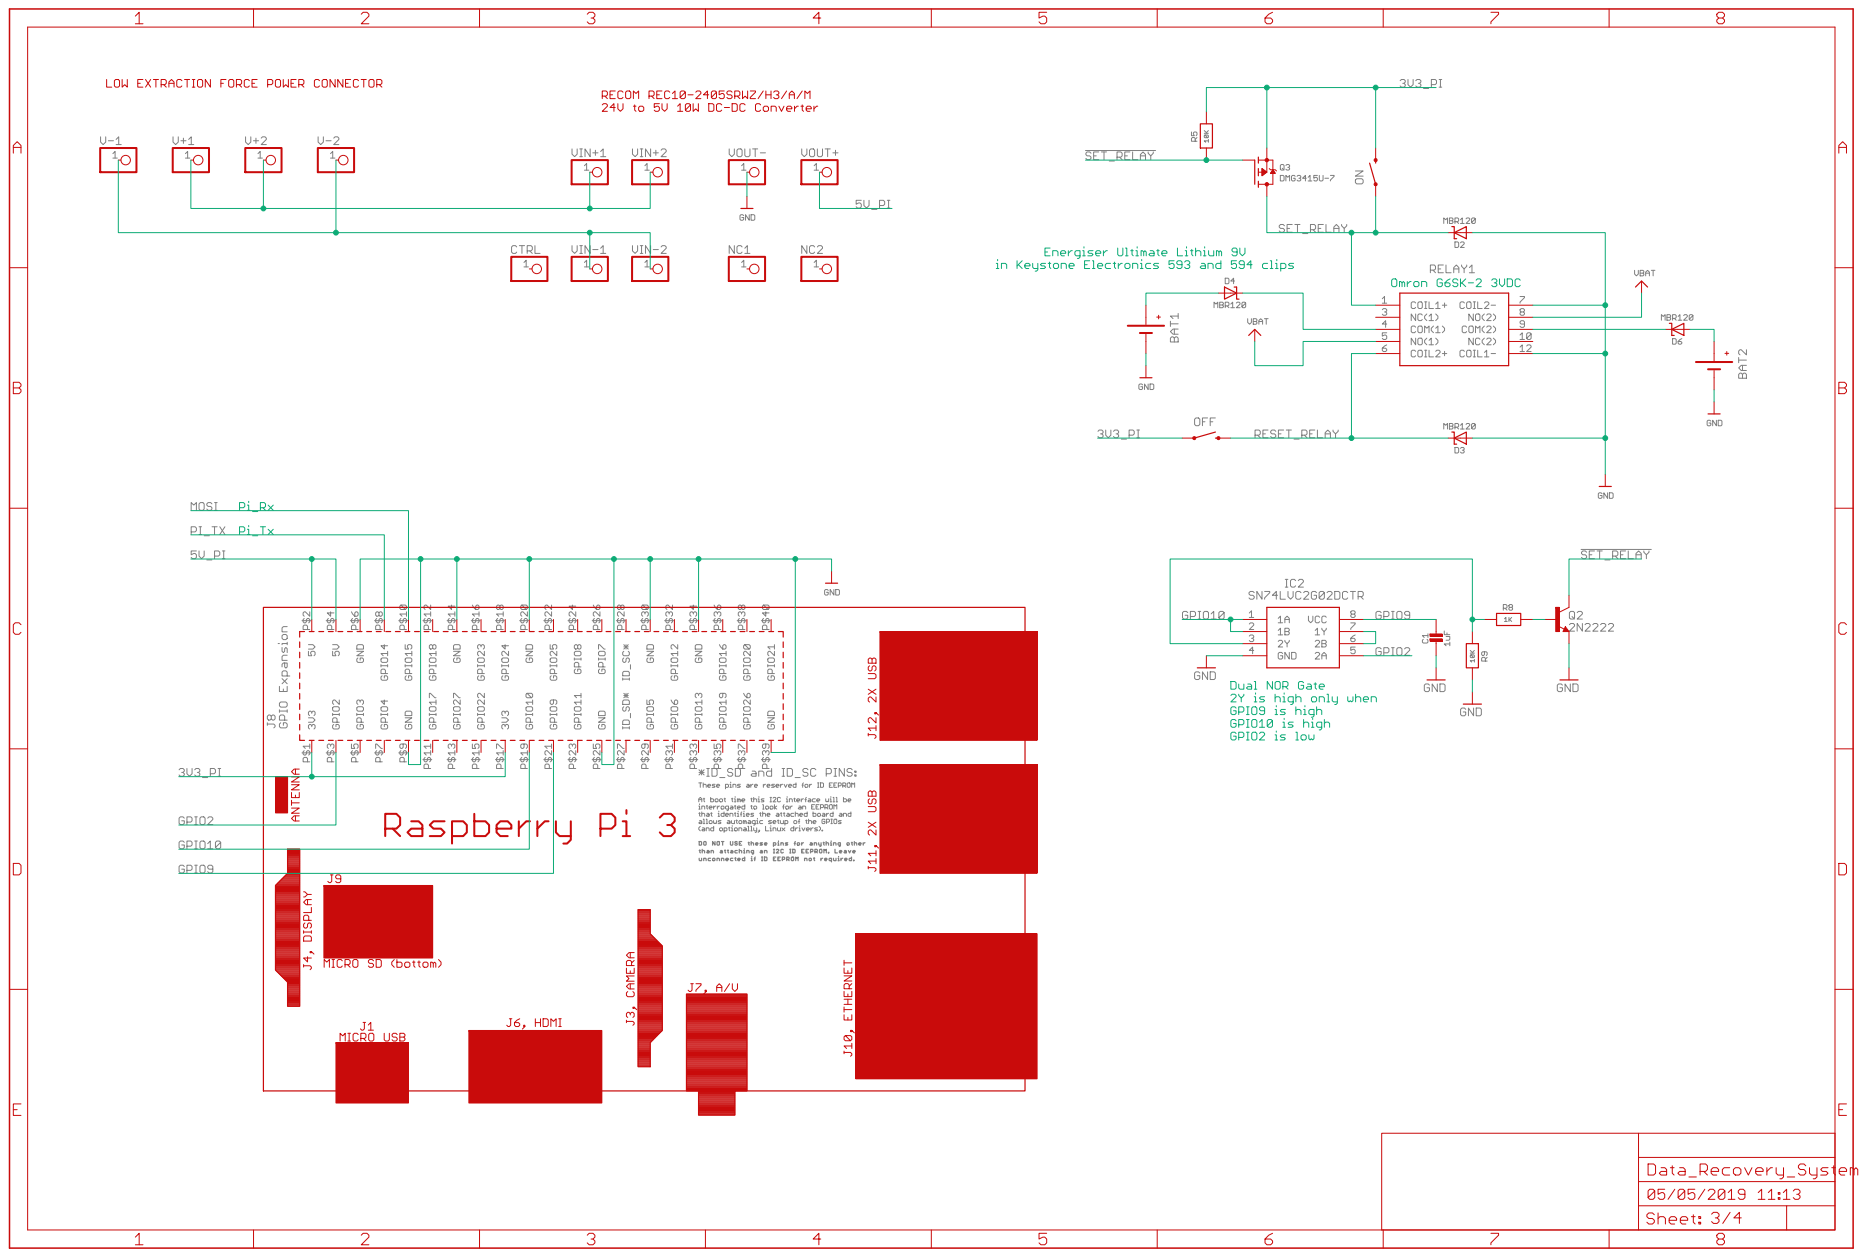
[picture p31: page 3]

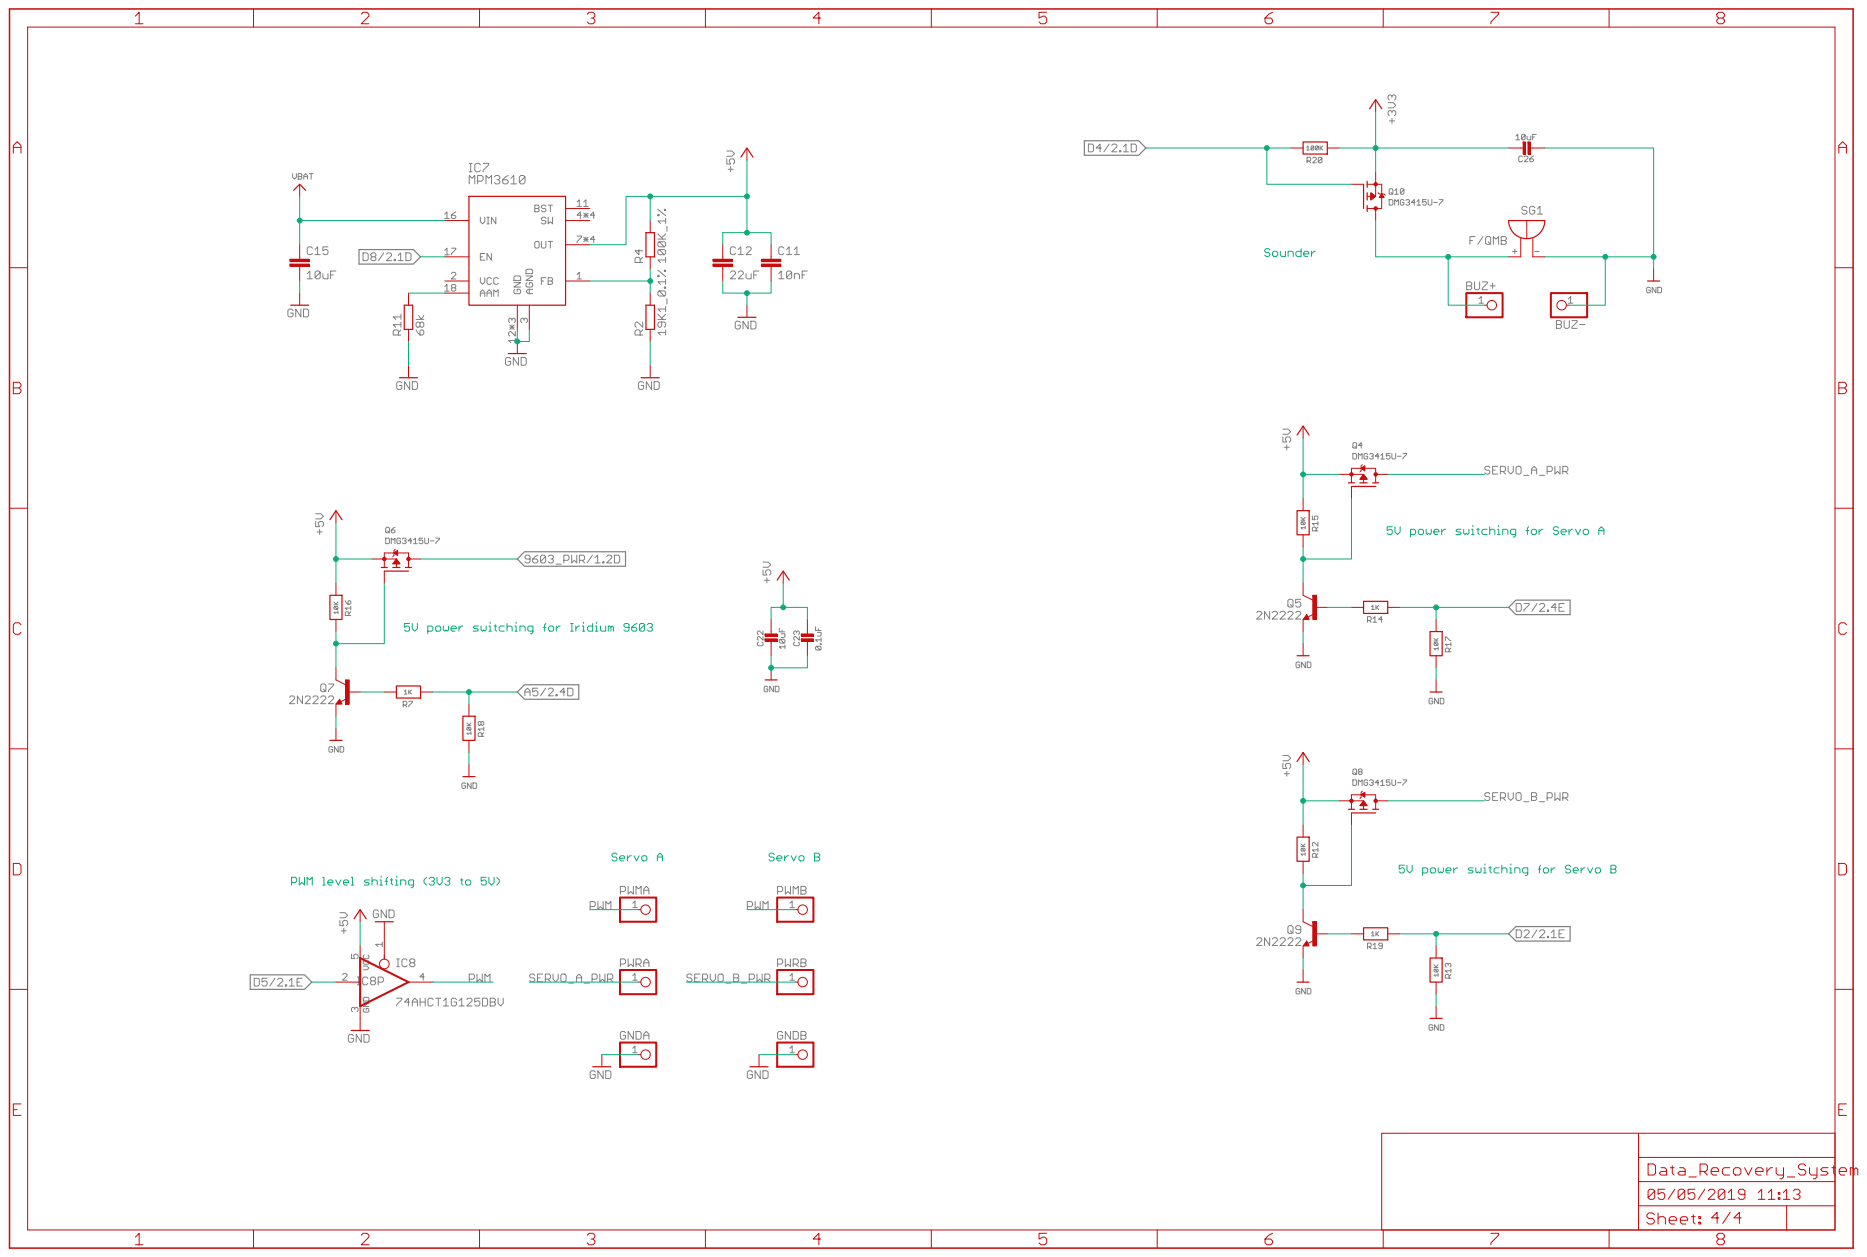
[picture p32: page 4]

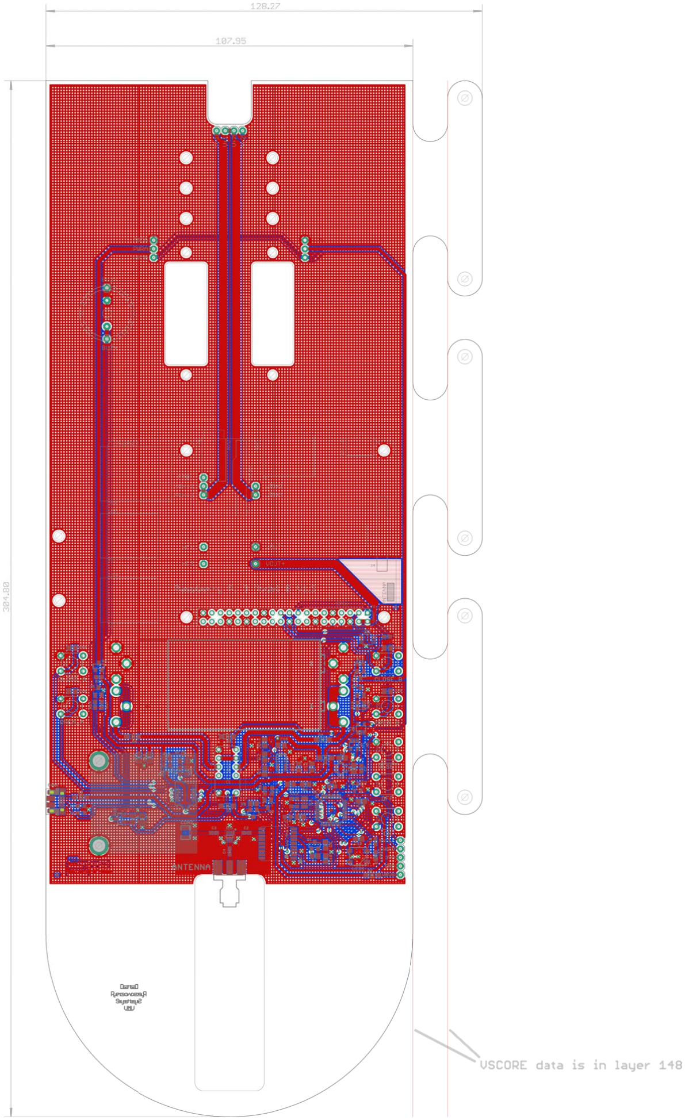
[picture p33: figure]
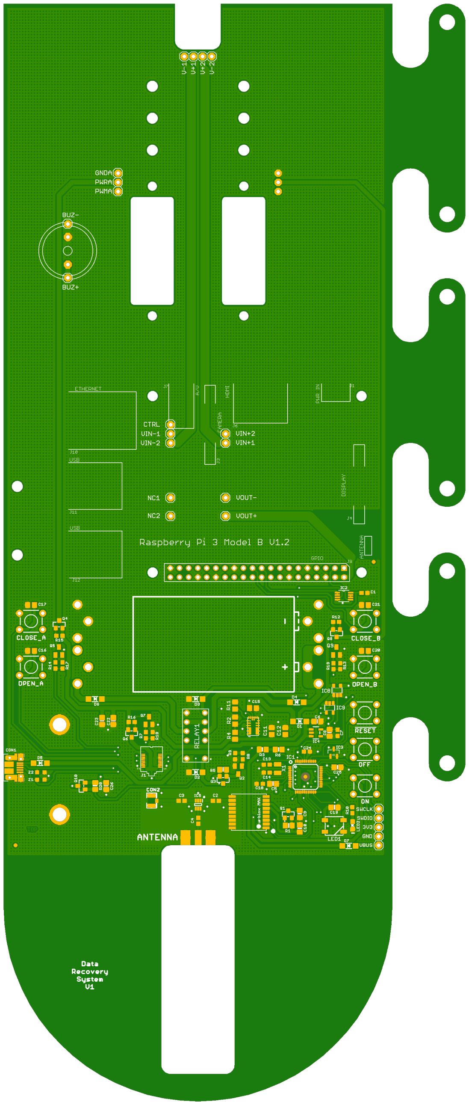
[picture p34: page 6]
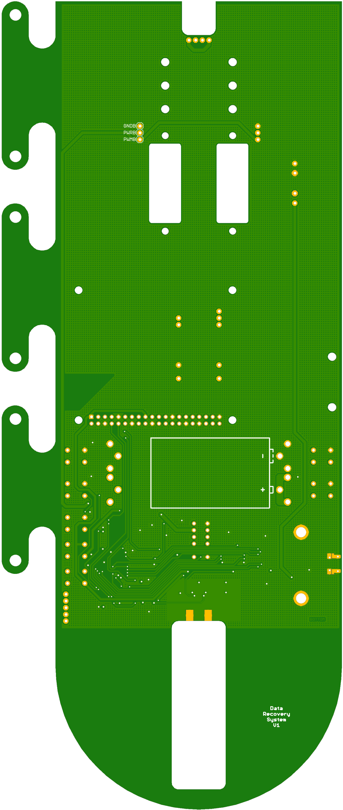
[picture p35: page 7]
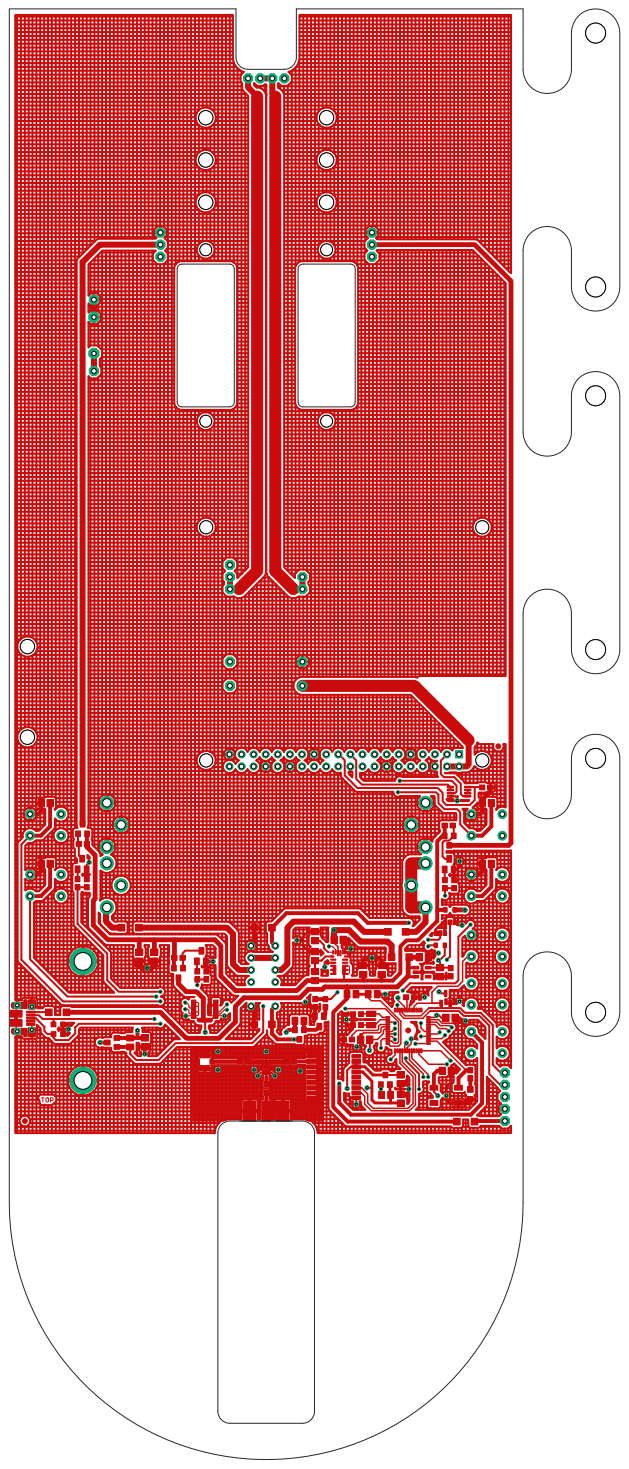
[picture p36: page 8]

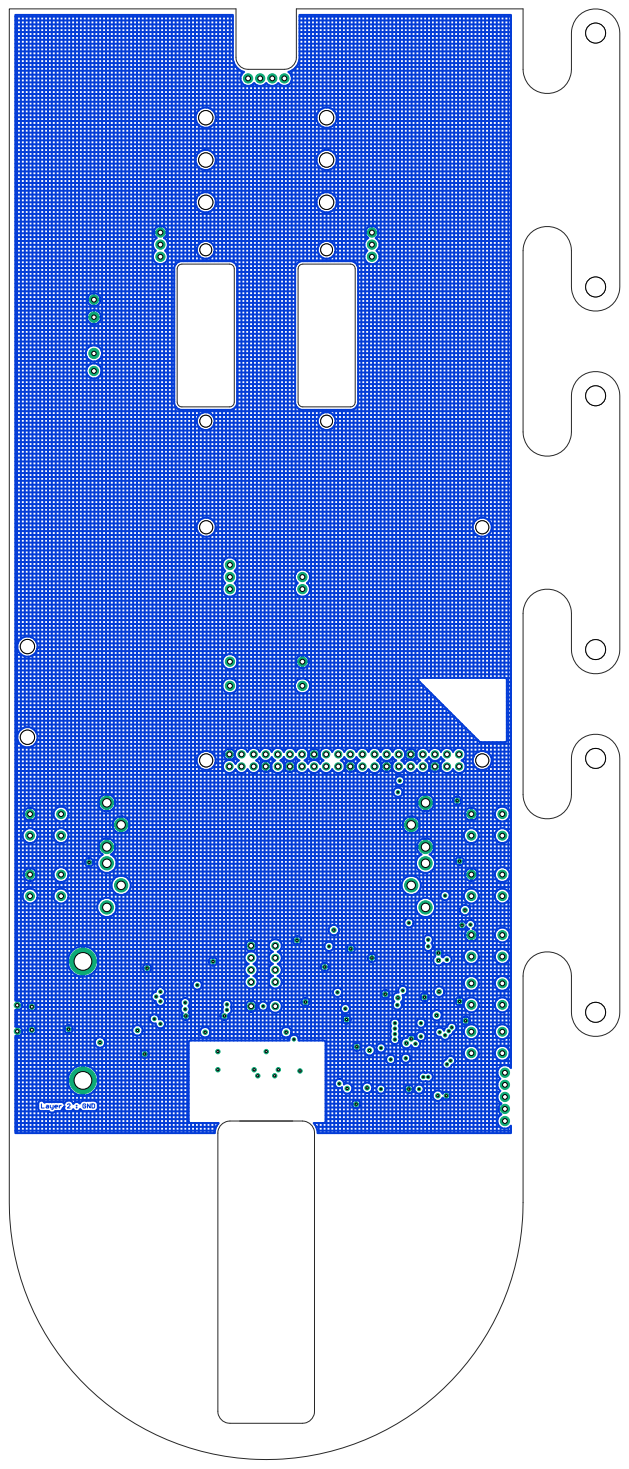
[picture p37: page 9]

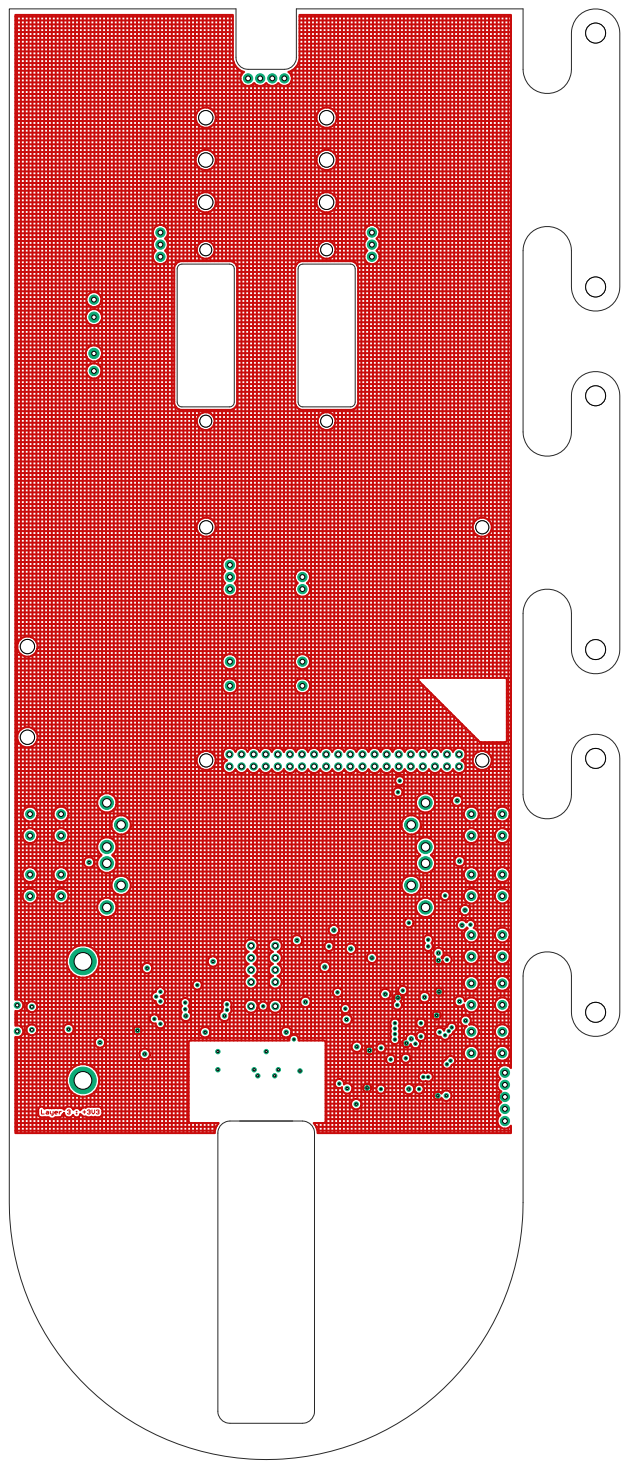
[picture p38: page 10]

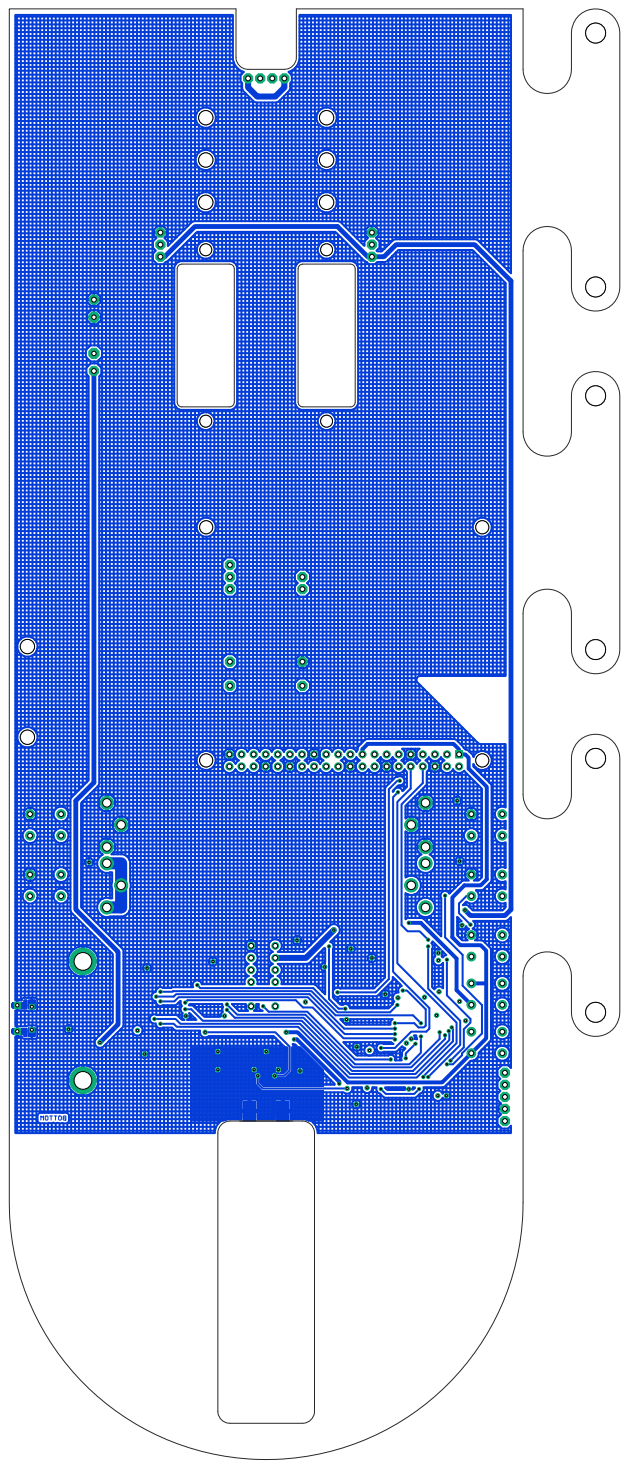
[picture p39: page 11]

Part | X | Y | Angle Package | Value | Manufacturer | Manufacturer Part No

Farnell Part
No | Mouser Part No | McMaster Part No | Description | Alternative Part
Dimensions | 107.95 304.80 | Excludes snap-off servo linkage pieces

Fiducials - for solder paste mask alignment:

FD1 | 3.28 | 71.12 0 | | | | | | Fiducial 1mm
FD2 | 102.75 149.86 0 | Fiducial 1mm

Surface Mount Components:

C1 | 100.2 141.22 | 0 0603 | 1uF | Walsin | 0603X105K100CT | 2496916 | MultiLayer Ceramic Capacitor; 1uF; 10V; 0603; X5R | 1uF 50V ±10% 0603 Samsung
C2 | 58.93 83.57 | 0 0603 | 120pF | Walsin | 0603B121K500CT | 2524820 | MultiLayer Ceramic Capacitor; 120pF; 50V; 0603
C3 | 49.4 83.57 | 180 0603 | 120pF | Walsin | 0603B121K500CT | 2524820 | MultiLayer Ceramic Capacitor; 120pF; 50V; 0603
C4 | 53.98 77.98 | 90 0603 | 120pF | Walsin | 0603B121K500CT | 2524820 | MultiLayer Ceramic Capacitor; 120pF; 50V; 0603
C5 | 74.8 88.27 | 180 0805 | 0.1uF | Walsin | 0805B104K500CT | 2496944 | MultiLayer Ceramic Capacitor; 0.1uF; 50V; 0805; X7R | 100nF 50V ±10% 0805 Samsung
C6 | 87.1 105.54 | 0 0805 | 10uF | Walsin | 0805F106Z100CT | 2496998 | MultiLayer Ceramic Capacitor; 10uF; 10V; 0805 | 10uF 16V ±10% 0805 Samsung
C7 | 92.75 102.39 | 270 0603 | 1uF | Walsin | 0603X105K100CT | 2496916 | MultiLayer Ceramic Capacitor; 1uF; 10V; 0603; X5R | 1uF 50V ±10% 0603 Samsung
C8 | 90.53 102.39 | 270 0805 | 10uF | Walsin | 0805F106Z100CT | 2496998 | MultiLayer Ceramic Capacitor; 10uF; 10V; 0805 | 10uF 16V ±10% 0805 Samsung
C9 | 82.2 79.86 | 270 0805 | 0.1uF | Walsin | 0805B104K500CT | 2496944 | MultiLayer Ceramic Capacitor; 0.1uF; 50V; 0805; X7R | 100nF 50V ±10% 0805 Samsung
C10 | 82.26 75.84 | 90 0805 | 10uF | Walsin | 0805F106Z100CT | 2496998 | MultiLayer Ceramic Capacitor; 10uF; 10V; 0805 | 10uF 16V ±10% 0805 Samsung
C11 | 74.4 102.87 | 90 0805 | 10nF | Walsin | 0805B103K500CT | 2496939 | MultiLayer Ceramic Capacitor; 10nF; 50V; 0805; X7R | 10nF 50V ±5% 0805 Samsung
C12 | 78.21 102.87 | 90 0805 | 10uF | Walsin | 0805F106Z100CT | 2496998 | MultiLayer Ceramic Capacitor; 10uF; 10V; 0805 | 10uF 16V ±10% 0805 Samsung
C13 | 73.03 | 93.6 | 180 0603 | 12pF | Walsin | 0603N120J500CT | 2496884 | MultiLayer Ceramic Capacitor; 12pF; 50V; 0603 | 12pF 50V ±5% 0603 Samsung
C14 | 73.03 91.31 | 180 0603 | 12pF | Walsin | 0603N120J500CT | 2496884 | MultiLayer Ceramic Capacitor; 12pF; 50V; 0603 | 12pF 50V ±5% 0603 Samsung
C15 | 69.19 109.22 | 0 0805 | 10uF | Walsin | 0805F106Z100CT | 2496998 | MultiLayer Ceramic Capacitor; 10uF; 10V; 0805 | 10uF 16V ±10% 0805 Samsung
C16 | 7.62 125.2 | 0 0805 | 10nF | Walsin | 0805B103K500CT | 2496939 | MultiLayer Ceramic Capacitor; 10nF; 50V; 0805; X7R | 10nF 50V ±5% 0805 Samsung
C17 | 7.62 137.9 | 0 0805 | 10nF | Walsin | 0805B103K500CT | 2496939 | MultiLayer Ceramic Capacitor; 10nF; 50V; 0805; X7R | 10nF 50V ±5% 0805 Samsung
C18 | 71.12 88.27 | 180 0603 | 1uF | Walsin | 0603X105K100CT | 2496916 | MultiLayer Ceramic Capacitor; 1uF; 10V; 0603; X5R | 1uF 50V ±10% 0603 Samsung
C19 | 91.89 81.69 | 0 0805 | 10uF | Walsin | 0805F106Z100CT | 2496998 | MultiLayer Ceramic Capacitor; 10uF; 10V; 0805 | 10uF 16V ±10% 0805 Samsung
C20 | 100.33 125.2 | 0 0805 | 10nF | Walsin | 0805B103K500CT | 2496939 | MultiLayer Ceramic Capacitor; 10nF; 50V; 0805; X7R | 10nF 50V ±5% 0805 Samsung
C21 | 100.33 137.9 | 0 0805 | 10nF | Walsin | 0805B103K500CT | 2496939 | MultiLayer Ceramic Capacitor; 10nF; 50V; 0805; X7R | 10nF 50V ±5% 0805 Samsung
C22 | 30.48 105.69 | 270 0805 | 10uF | Walsin | 0805F106Z100CT | 2496998 | MultiLayer Ceramic Capacitor; 10uF; 10V; 0805 | 10uF 16V ±10% 0805 Samsung
C23 | 27.3 105.69 | 270 0805 | 0.1uF | Walsin | 0805B104K500CT | 2496944 | MultiLayer Ceramic Capacitor; 0.1uF; 50V; 0805; X7R | 100nF 50V ±10% 0805 Samsung
C24 | 84.2 97.16 | 0 0603 | 1uF | Walsin | 0603X105K100CT | 2496916 | MultiLayer Ceramic Capacitor; 1uF; 10V; 0603; X5R | 1uF 50V ±10% 0603 Samsung
C25 | 92.71 92.84 | 0 0805 | 10uF | Walsin | 0805F106Z100CT | 2496998 | MultiLayer Ceramic Capacitor; 10uF; 10V; 0805 | 10uF 16V ±10% 0805 Samsung
C26 | 28.45 87.63 | 270 0805 | 10uF | Walsin | 0805F106Z100CT | 2496998 | MultiLayer Ceramic Capacitor; 10uF; 10V; 0805 | 10uF 16V ±10% 0805 Samsung
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

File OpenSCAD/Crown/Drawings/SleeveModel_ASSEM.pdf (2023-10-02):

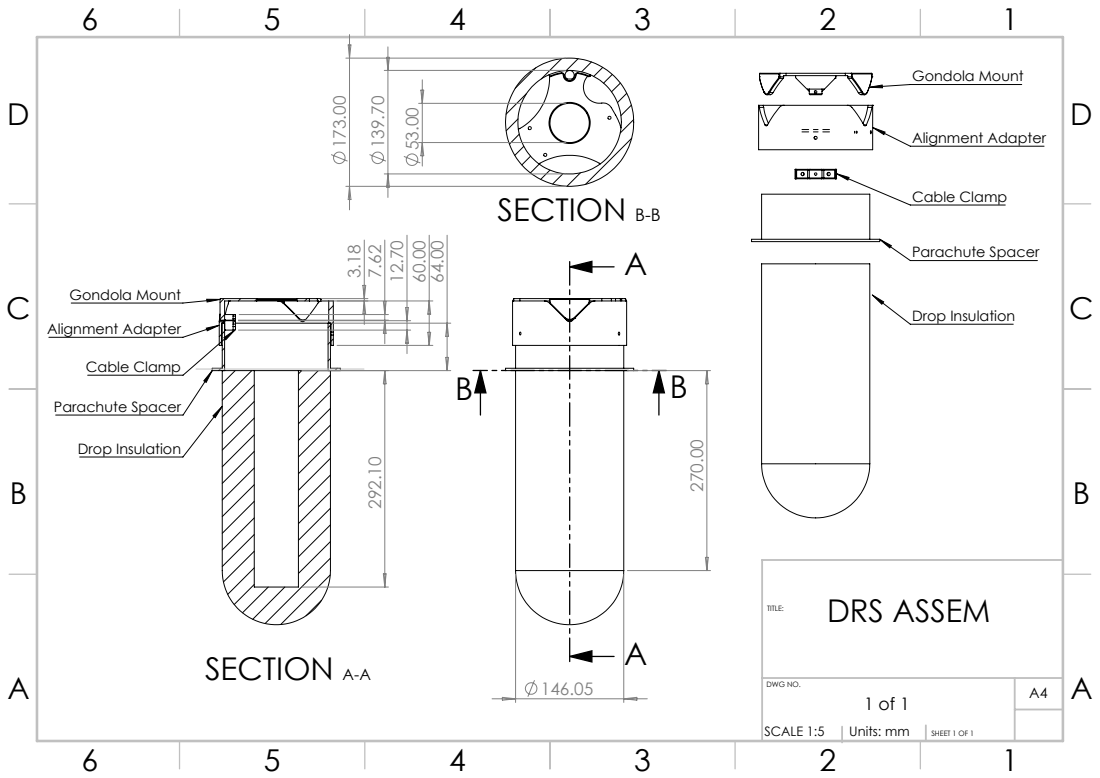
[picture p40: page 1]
Drop Insulation; Parachute Spacer; Cable Clamp; Alignment Adapter; Gondola Mount; SECTION A-A173.00; SECTION B-B; DWG NO.; SCALE 1:5; SHEET 1 OF 1; DRS ASSEM; Units: mm

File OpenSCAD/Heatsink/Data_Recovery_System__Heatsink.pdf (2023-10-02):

Designed by; Checked by; Approved by; Date

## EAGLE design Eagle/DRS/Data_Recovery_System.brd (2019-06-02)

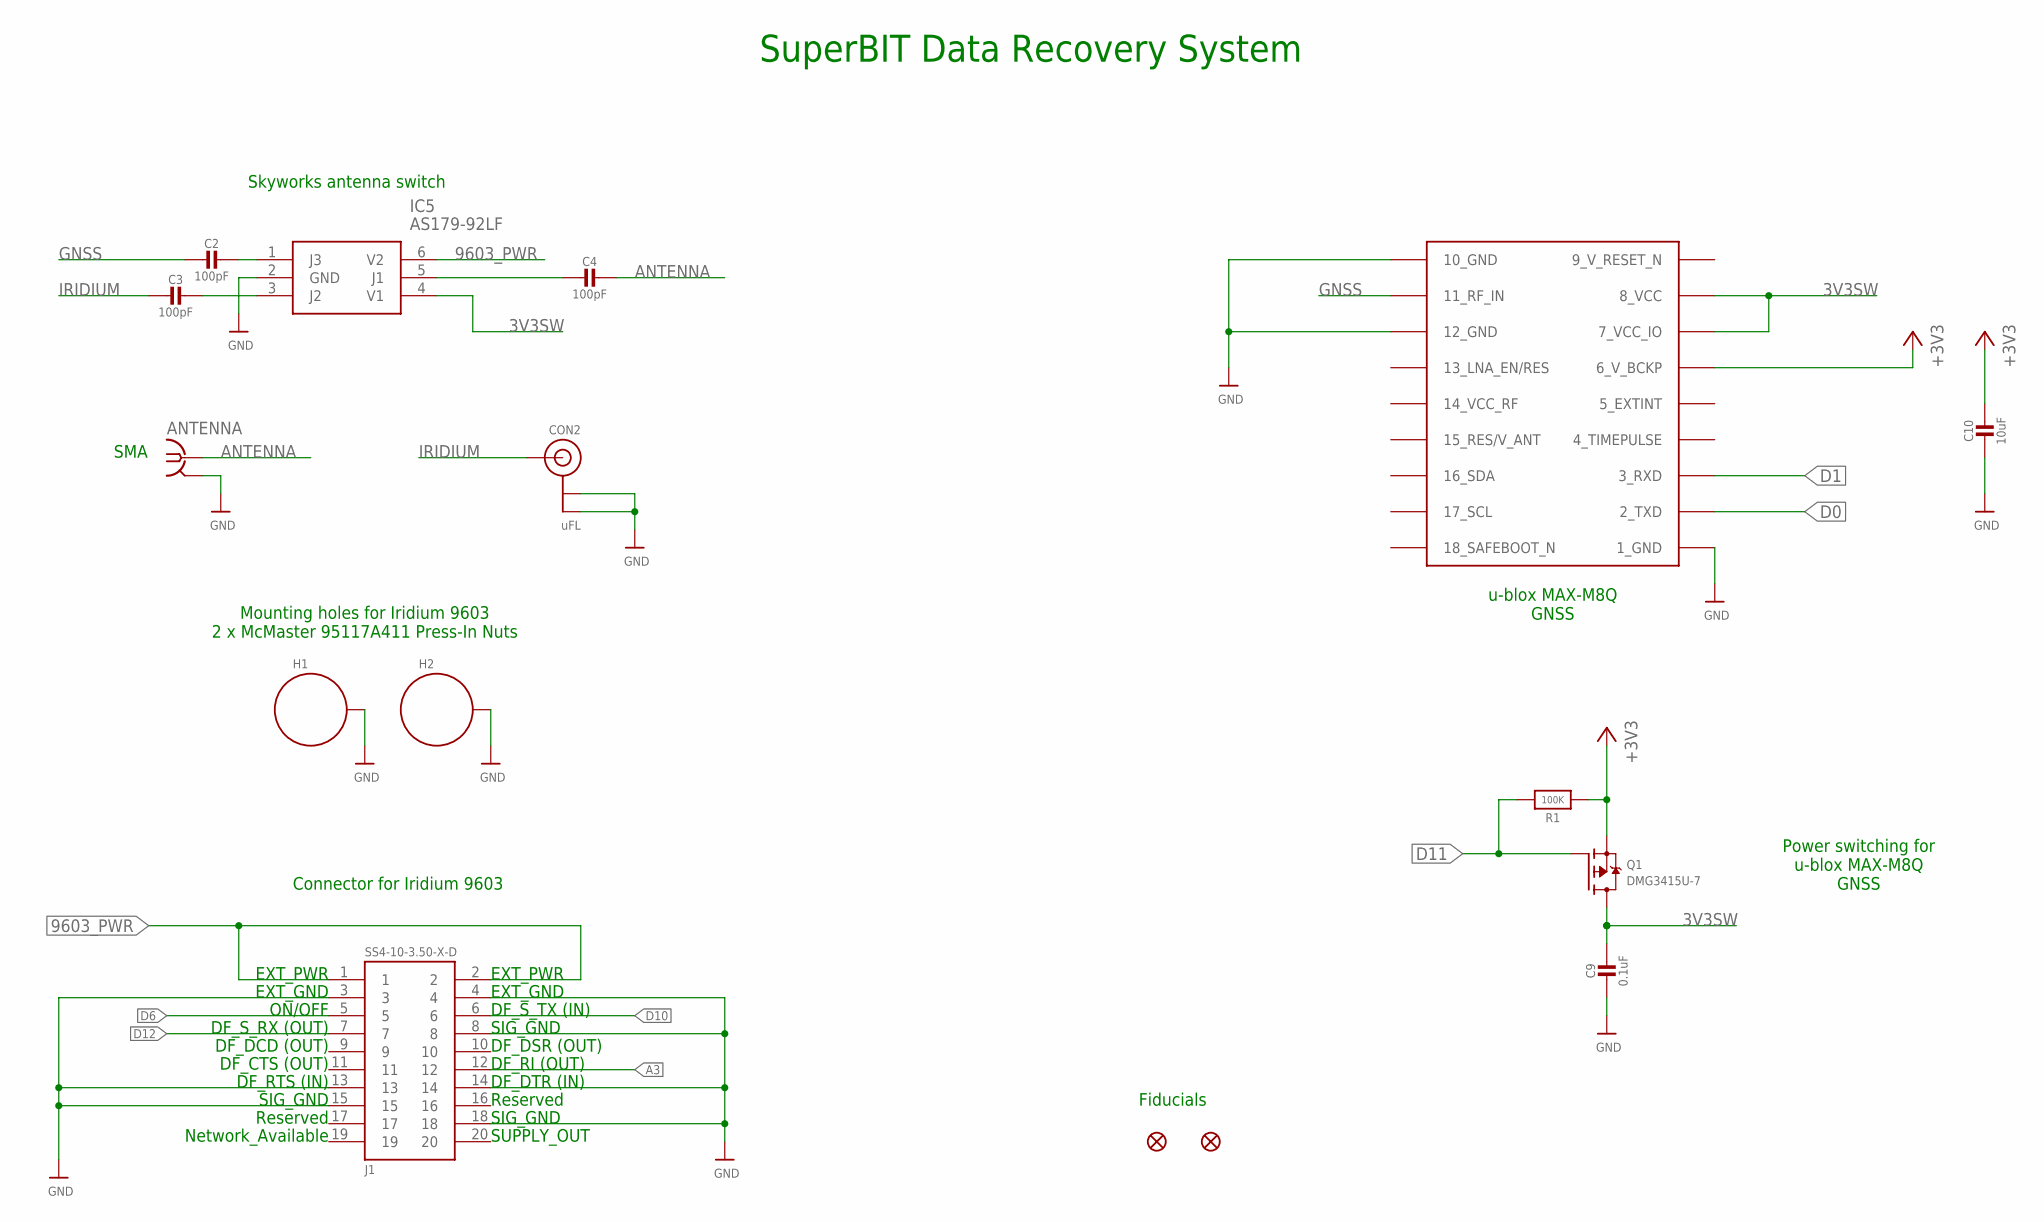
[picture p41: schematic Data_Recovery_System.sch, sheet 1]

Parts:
ANTENNA: SMA-142-0711-821/826; J502-ND-142-0711-821/826
C2, C3, C4: 100pF; 0603-NO@1
C9: 0.1uF; 0805-NO@1
C10: 10uF; 0805-NO@1
CON2: uFL; U.FL
FD1, FD2: FIDUCIAL1X2; FIDUCIAL-1X2
H1, H2: STANDOFF_ELECTRICALMCMASTER-95117A411; STANDOFF-ELECTRICAL-MCMASTER-95117A411
IC5: AS179-92LF; SOT65P220X100-6N
IC6: MAX-M8
J1: SS4-10-3.50-X-D
Q1: DMG3415U-7; SOT23-WIDE
R1: 100K; 0805-NO

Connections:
3V3SW: C9.1, IC5.4 (V1), IC6.7_VCC_IO, IC6.8_VCC, Q1.3 (D)
9_V_RESET_N: IC6.9_RESET_N (9_V_RESET_N)
9603_PWR: IC5.6 (V2), J1.1, J1.2; also elsewhere on the board
+3V3: C10.1, IC6.6_V_BCKP, Q1.2 (S), R1.1; also elsewhere on the board
A3: J1.12; also elsewhere on the board
ANTENNA: ANTENNA.1, C4.1
D0: IC6.2_TXD; also elsewhere on the board
D1: IC6.3_RXD; also elsewhere on the board
D6: J1.5; also elsewhere on the board
D10: J1.6; also elsewhere on the board
D11: Q1.1 (G), R1.2; also elsewhere on the board
D12: J1.7; also elsewhere on the board
GND: ANTENNA.G@1 (2), ANTENNA.G@2 (2), ANTENNA.G@3 (2), ANTENNA.G@4 (2), C9.2, C10.2, CON2.1 (GND), CON2.2 (GND), H1.P1, H2.P1, IC5.2 (GND), IC6.1_GND, IC6.10_GND, IC6.12_GND, J1.3, J1.4, J1.8, J1.13, J1.14, J1.15, J1.18; also elsewhere on the board
GNSS: C2.2, IC6.11_RF_IN
IRIDIUM: C3.2, CON2.3 (SIGNAL)
unnamed: C2.1, IC5.1 (J3)
unnamed: C3.1, IC5.3 (J2)
unnamed: C4.2, IC5.5 (J1)

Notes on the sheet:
Connector for Iridium 9603
Mounting holes for Iridium 9603 2 x McMaster 95117A411 Press-In Nuts
SuperBIT Data Recovery System
EXT_PWR
EXT_GND
ON/OFF
DF_S_RX (OUT)
DF_DCD (OUT)
DF_CTS (OUT)
DF_RTS (IN)
SIG_GND
Reserved
Network_Available
DF_S_TX (IN)
DF_DSR (OUT)
DF_RI (OUT)
DF_DTR (IN)
SUPPLY_OUT
Fiducials
u-blox MAX-M8Q GNSS
Power switching for u-blox MAX-M8Q GNSS
Skyworks antenna switch
SMA

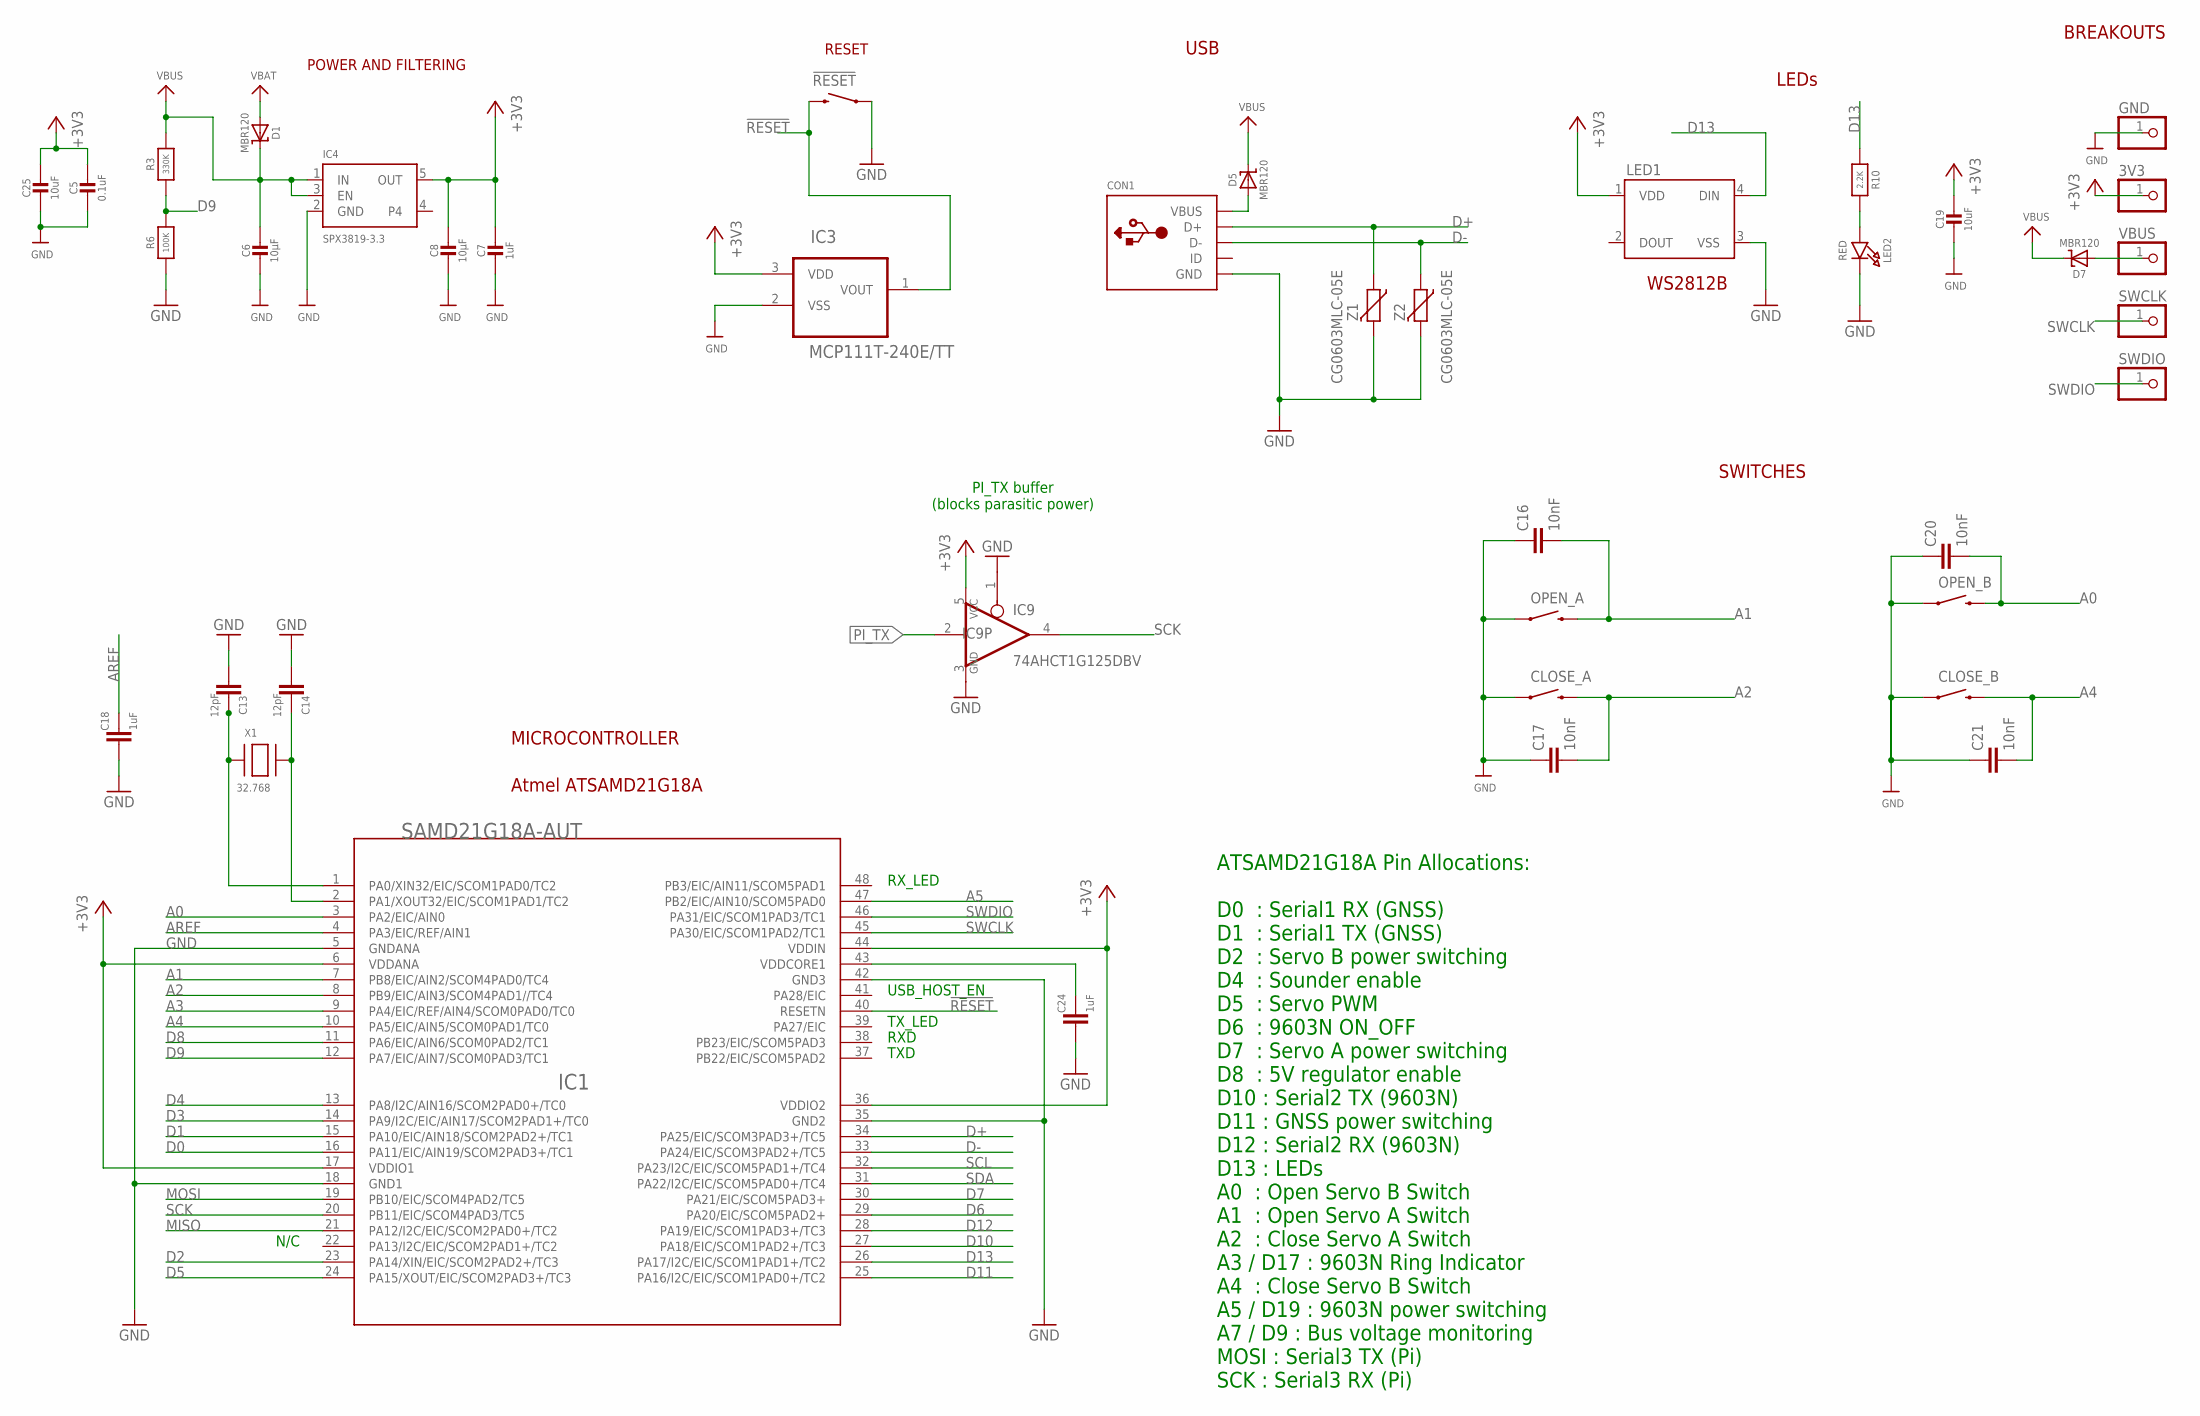
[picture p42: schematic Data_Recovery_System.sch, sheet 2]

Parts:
3V3: PINHD-1X1; 1X01
!RESET: SWITCH-MOMENTARY-2PTH; TACTILE-PTH
C5: 0.1uF; 0805-NO@1
C6, C8: 10µF; 0805-NO@1
C7: 1uF; 0603-NO@1
C13, C14: 12pF; C0603
C16, C17, C20, C21: 10nF; C0805
C18, C24: 1uF; C0603
C19, C25: 10uF; 0805-NO@1
CLOSE_A: SWITCH-MOMENTARY-2PTH; TACTILE-PTH
CLOSE_B: SWITCH-MOMENTARY-2PTH; TACTILE-PTH
CON1: MICROBUILDER_USBFCI_10103594_CORRECTED; MICROBUILDER_FCI_10103594_CORRECTED
D1, D5, D7: MBR120; SOD-123
GND: PINHD-1X1; 1X01
IC1: SAMD21G18A-AUT; TQFP48-7X7
IC3: MCP111T-240E/TT; SOT95P237X112-3N; MPN MCP111T-240E/TT
IC4: SPX3819-3.3; SOT23-5
IC9: 74AHCT1G125DBV; SOT23-5
LED1: WS2812B
LED2: RED; CHIPLED_0805_NOOUTLINE
OPEN_A: SWITCH-MOMENTARY-2PTH; TACTILE-PTH
OPEN_B: SWITCH-MOMENTARY-2PTH; TACTILE-PTH
R3: 330K; 0805-NO
R6: 100K; 0805-NO
R10: 2.2K; 0603-NO
SWCLK: PINHD-1X1; 1X01
SWDIO: PINHD-1X1; 1X01
VBUS: PINHD-1X1; 1X01
X1: 32.768; XTAL3215
Z1, Z2: CG0603MLC-05E; CT/CN0603

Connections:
!RESET: !RESET.3 (2), IC1.40 (RESETN), IC3.1 (VOUT)
+3V3: 3V3.1, C5.1, C7.1, C8.1, C19.1, C25.1, IC1.6 (VDDANA), IC1.17 (VDDIO1), IC1.36 (VDDIO2), IC1.44 (VDDIN), IC3.3 (VDD), IC4.5 (OUT), IC9.5 (VCC), LED1.1 (VDD); also elsewhere on the board
A0: C20.2, IC1.3 (PA2/EIC/AIN0), OPEN_B.3 (2)
A1: C16.2, IC1.7 (PB8/EIC/AIN2/SCOM4PAD0/TC4), OPEN_A.3 (2)
A2: C17.2, CLOSE_A.3 (2), IC1.8 (PB9/EIC/AIN3/SCOM4PAD1//TC4)
A3: IC1.9 (PA4/EIC/REF/AIN4/SCOM0PAD0/TC0); also elsewhere on the board
A4: C21.2, CLOSE_B.3 (2), IC1.10 (PA5/EIC/AIN5/SCOM0PAD1/TC0)
A5: IC1.47 (PB2/EIC/AIN10/SCOM5PAD0); also elsewhere on the board
AREF: C18.1, IC1.4 (PA3/EIC/REF/AIN1)
D0: IC1.16 (PA11/EIC/AIN19/SCOM2PAD3+/TC1); also elsewhere on the board
D1: IC1.15 (PA10/EIC/AIN18/SCOM2PAD2+/TC1); also elsewhere on the board
D2: IC1.23 (PA14/XIN/EIC/SCOM2PAD2+/TC3); also elsewhere on the board
D3: IC1.14 (PA9/I2C/EIC/AIN17/SCOM2PAD1+/TC0)
D4: IC1.13 (PA8/I2C/AIN16/SCOM2PAD0+/TC0); also elsewhere on the board
D5: IC1.24 (PA15/XOUT/EIC/SCOM2PAD3+/TC3); also elsewhere on the board
D6: IC1.29 (PA20/EIC/SCOM5PAD2+); also elsewhere on the board
D7: IC1.30 (PA21/EIC/SCOM5PAD3+); also elsewhere on the board
D8: IC1.11 (PA6/EIC/AIN6/SCOM0PAD2/TC1); also elsewhere on the board
D9: IC1.12 (PA7/EIC/AIN7/SCOM0PAD3/TC1), R3.1, R6.2
D10: IC1.27 (PA18/EIC/SCOM1PAD2+/TC3); also elsewhere on the board
D11: IC1.25 (PA16/I2C/EIC/SCOM1PAD0+/TC2); also elsewhere on the board
D12: IC1.28 (PA19/EIC/SCOM1PAD3+/TC3); also elsewhere on the board
D13: IC1.26 (PA17/I2C/EIC/SCOM1PAD1+/TC2), LED1.4 (DIN), R10.1
D+: CON1.D+, IC1.34 (PA25/EIC/SCOM3PAD3+/TC5), Z1.1
D-: CON1.D-, IC1.33 (PA24/EIC/SCOM3PAD2+/TC5), Z2.1
GND: !RESET.1, C5.2, C6.2, C7.2, C8.2, C13.2, C14.2, C16.1, C17.1, C18.2, C19.2, C20.1, C21.1, C24.2, C25.2, CLOSE_A.1, CLOSE_B.1, CON1.BASE@1 (GND), CON1.BASE@2 (GND), CON1.GND, CON1.SPRT@1 (GND), CON1.SPRT@2 (GND), CON1.SPRT@3 (GND), CON1.SPRT@4 (GND), GND.1, IC1.5 (GNDANA), IC1.18 (GND1), IC1.35 (GND2), IC1.42 (GND3), IC3.2 (VSS), IC4.2 (GND), IC9.1 (OE), IC9.3 (GND), LED1.3 (VSS), LED2.C, OPEN_A.1, OPEN_B.1, R6.1, Z1.2, Z2.2; also elsewhere on the board
MISO: IC1.21 (PA12/I2C/EIC/SCOM2PAD0+/TC2)
MOSI: IC1.19 (PB10/EIC/SCOM4PAD2/TC5); also elsewhere on the board
unnamed: C13.1, IC1.1 (PA0/XIN32/EIC/SCOM1PAD0/TC2), X1.P$1
unnamed: C14.1, IC1.2 (PA1/XOUT32/EIC/SCOM1PAD1/TC2), X1.P$2
unnamed: LED2.A, R10.2
unnamed: CON1.VBUS, D5.A
unnamed: D7.A, VBUS.1
PI_TX: IC9.2 (I); also elsewhere on the board
SCK: IC1.20 (PB11/EIC/SCOM4PAD3/TC5), IC9.4 (O)
SCL: IC1.32 (PA23/I2C/EIC/SCOM5PAD1+/TC4)
SDA: IC1.31 (PA22/I2C/EIC/SCOM5PAD0+/TC4)
SWCLK: IC1.45 (PA30/EIC/SCOM1PAD2/TC1), SWCLK.1
SWDIO: IC1.46 (PA31/EIC/SCOM1PAD3/TC1), SWDIO.1
VBAT: D1.A; also elsewhere on the board
VBUS: C6.1, D1.C, D5.C, D7.C, IC4.1 (IN), IC4.3 (EN), R3.2
VDDCORE2: C24.1, IC1.43 (VDDCORE1)

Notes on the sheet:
MICROCONTROLLER
USB_HOST_EN
TXD
RXD
TX_LED
RX_LED
Atmel ATSAMD21G18A
N/C
POWER AND FILTERING
RESET
USB
BREAKOUTS
LEDs
WS2812B
SWITCHES
ATSAMD21G18A Pin Allocations: D0 : Serial1 RX (GNSS) D1 : Serial1 TX (GNSS) D2 : Servo B power switching D4 : Sounder enable D5 : Servo PWM D6 : 9603N ON_OFF D7 : Servo A power switching D8 : 5V regulator enable D10 : Serial2 TX (9603N) D11 : GNSS power switching D12 : Serial2 RX (9603N) D13 : LEDs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
PI_TX buffer (blocks parasitic power)

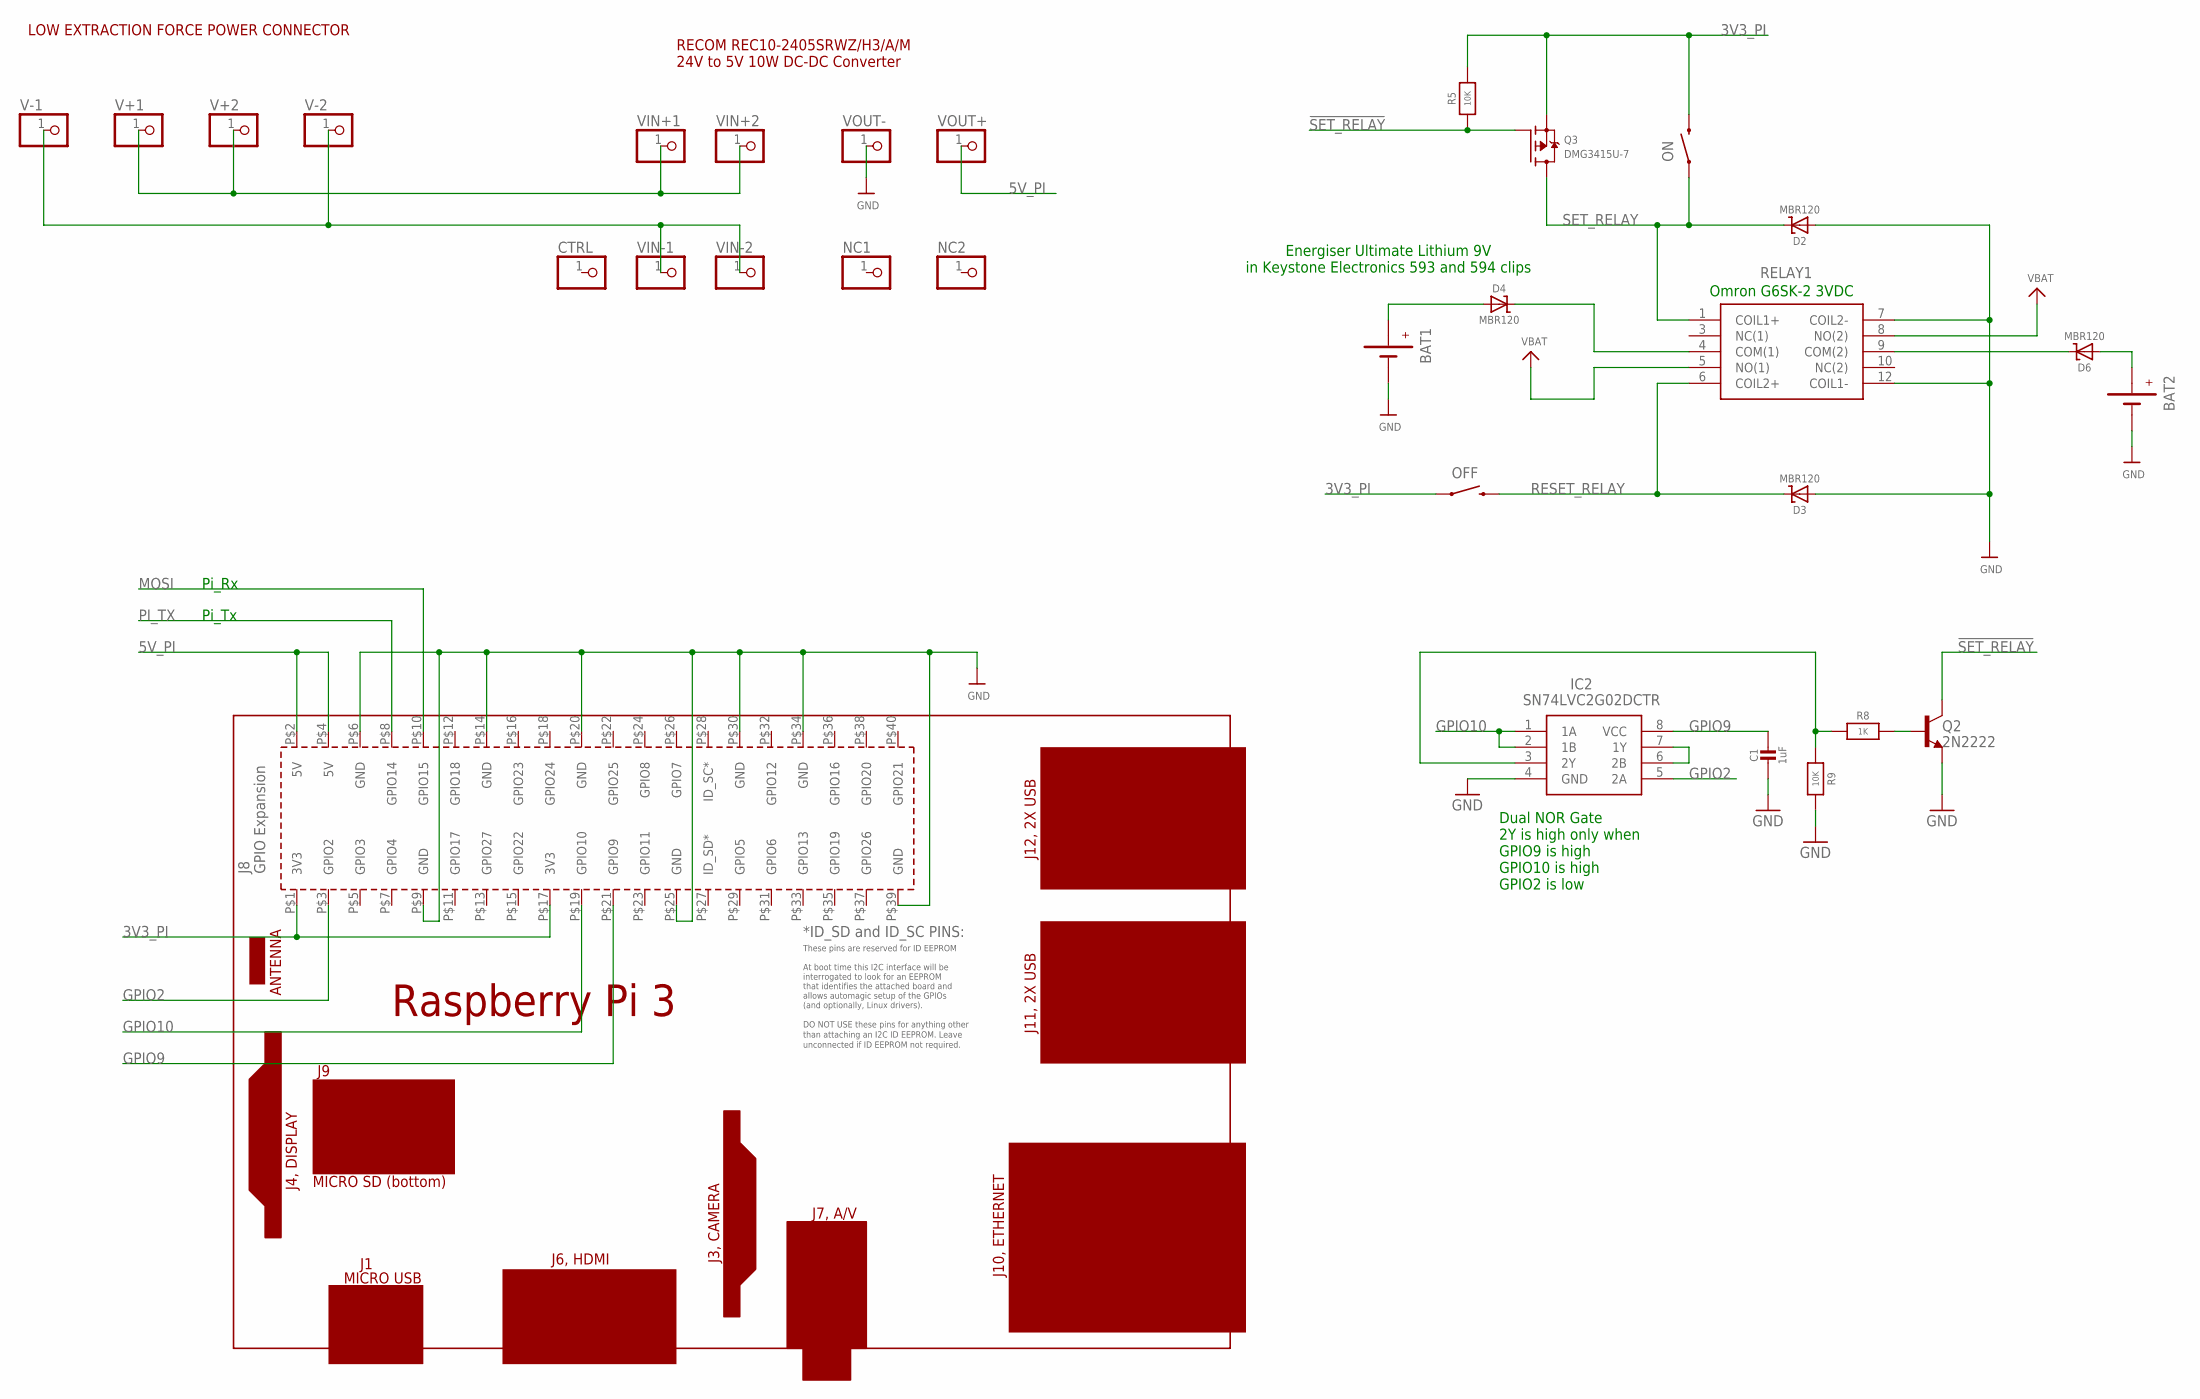
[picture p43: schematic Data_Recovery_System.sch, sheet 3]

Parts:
BAT1, BAT2: BATTERYBATTERY-9V-KEYSTONE-593-594; BATTERY-9V-KEYSTONE-593-594
C1: 1uF; 0603-NO@1
CTRL: PINHD-1X1; 1X01
D2, D3, D4, D6: MBR120; SOD-123
IC2: SN74LVC2G02DCTR; SOP65P400X130-8N
NC1, NC2: PINHD-1X1; 1X01
OFF: SWITCH-MOMENTARY-2PTH; TACTILE-PTH
ON: SWITCH-MOMENTARY-2PTH; TACTILE-PTH
PCB1: RPI3
Q2: 2N2222; SOT23-BEC
Q3: DMG3415U-7; SOT23-WIDE
R5: 10K; 0805-NO
R8: 1K; 0603-NO
R9: 10K; 0603-NO
RELAY1: G6SK-2_DC5; G6SK2DC5
V+1, V+2: PINHD-1X1; 1X01
V-1, V-2: PINHD-1X1; 1X01
VIN+1, VIN+2: PINHD-1X1; 1X01
VIN-1, VIN-2: PINHD-1X1; 1X01
VOUT+: PINHD-1X1; 1X01
VOUT-: PINHD-1X1; 1X01

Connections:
3V3_PI: OFF.1, ON.3 (2), PCB1.P$1 (3V3), PCB1.P$17 (3V3), Q3.2 (S), R5.2
5V_PI: PCB1.P$2 (5V), PCB1.P$4 (5V), VOUT+.1
!SET_RELAY: Q2.C, Q3.1 (G), R5.1
GND: BAT1.GND (-), BAT1.GND1 (-), BAT1.GND2 (-), BAT2.GND (-), BAT2.GND1 (-), BAT2.GND2 (-), C1.2, D2.A, D3.A, IC2.4 (GND), PCB1.P$6 (GND), PCB1.P$9 (GND), PCB1.P$14 (GND), PCB1.P$20 (GND), PCB1.P$25 (GND), PCB1.P$30 (GND), PCB1.P$34 (GND), PCB1.P$39 (GND), Q2.E, R9.2, RELAY1.7 (COIL2-), RELAY1.12 (COIL1-), VOUT-.1; also elsewhere on the board
GPIO2: IC2.5 (2A), PCB1.P$3 (GPIO2)
GPIO9: C1.1, IC2.8 (VCC), PCB1.P$21 (GPIO9)
GPIO10: IC2.1 (1A), IC2.2 (1B), PCB1.P$19 (GPIO10)
MOSI: PCB1.P$10 (GPIO15); also elsewhere on the board
unnamed: V-1.1, V-2.1, VIN-1.1, VIN-2.1
unnamed: D6.C, RELAY1.9 (COM(2))
unnamed: BAT2.PWR (+), BAT2.PWR1 (+), BAT2.PWR2 (+), D6.A
unnamed: BAT1.PWR (+), BAT1.PWR1 (+), BAT1.PWR2 (+), D4.A
unnamed: D4.C, RELAY1.4 (COM(1))
unnamed: Q2.B, R8.2
unnamed: IC2.3 (2Y), R8.1, R9.1
unnamed: IC2.6 (2B), IC2.7 (1Y)
PI_TX: PCB1.P$8 (GPIO14); also elsewhere on the board
RESET_RELAY: D3.C, OFF.3 (2), RELAY1.6 (COIL2+)
SET_RELAY: D2.C, ON.1, Q3.3 (D), RELAY1.1 (COIL1+)
VBAT: RELAY1.5 (NO(1)), RELAY1.8 (NO(2)); also elsewhere on the board
V_EXT: V+1.1, V+2.1, VIN+1.1, VIN+2.1

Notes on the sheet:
Omron G6SK-2 3VDC
Energiser Ultimate Lithium 9V in Keystone Electronics 593 and 594 clips
LOW EXTRACTION FORCE POWER CONNECTOR
RECOM REC10-2405SRWZ/H3/A/M 24V to 5V 10W DC-DC Converter
Dual NOR Gate 2Y is high only when GPIO9 is high GPIO10 is high GPIO2 is low
Pi_Tx
Pi_Rx

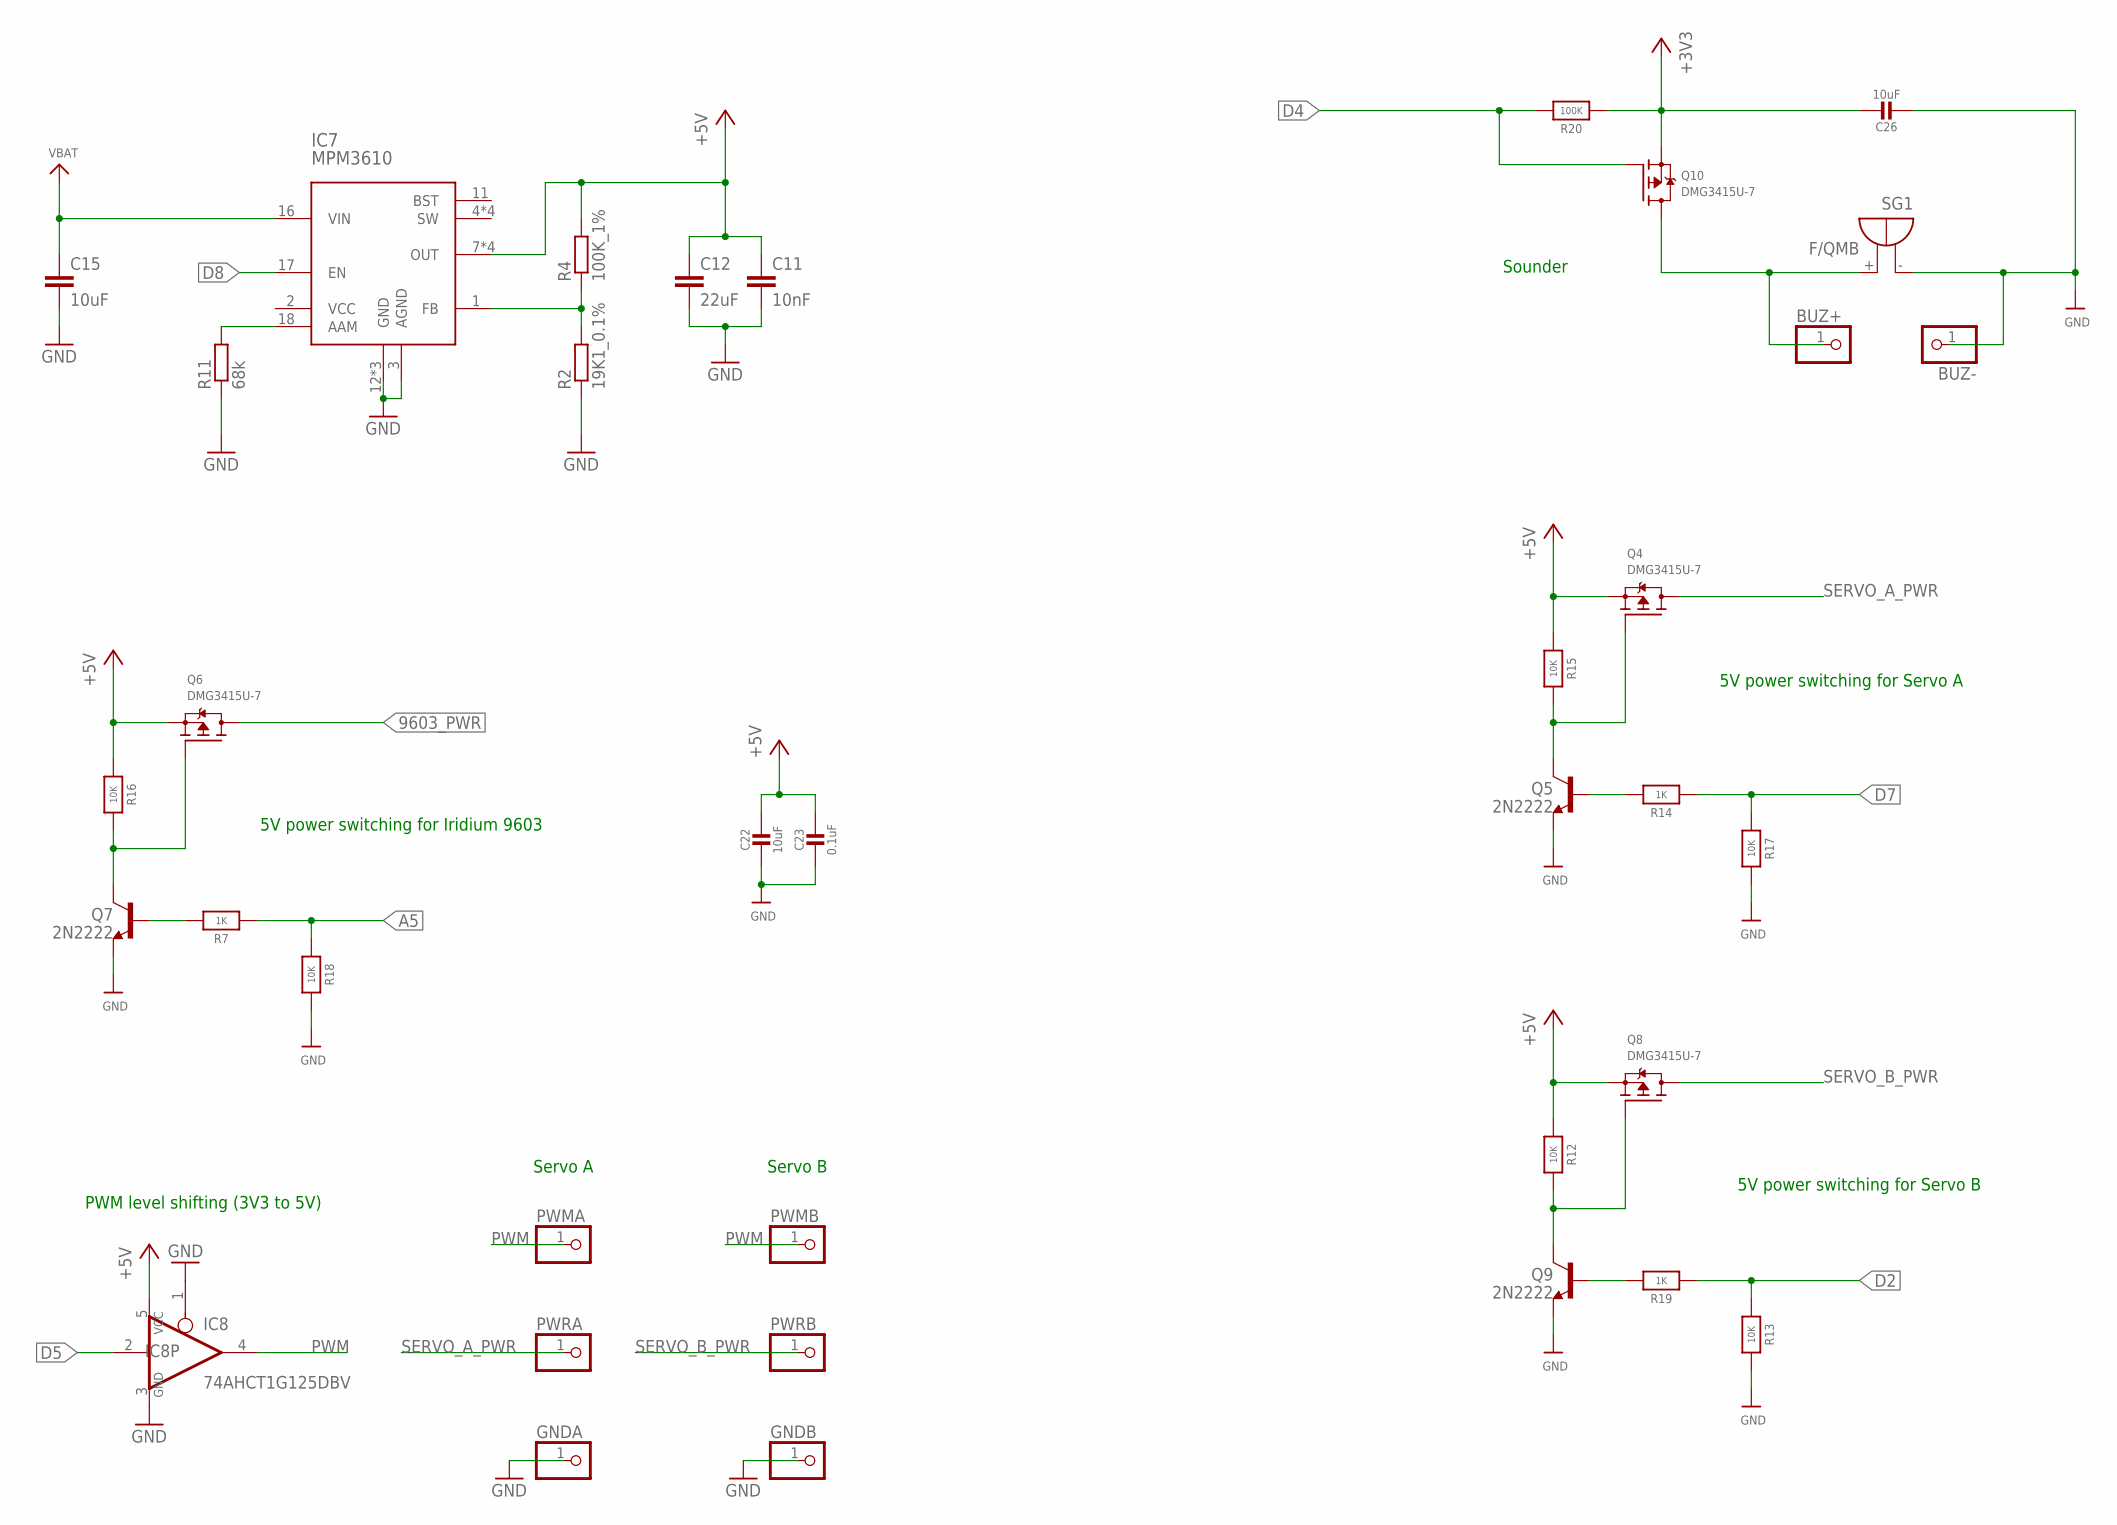
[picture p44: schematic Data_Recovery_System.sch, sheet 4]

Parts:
BUZ+: PINHD-1X1; 1X01
BUZ-: PINHD-1X1; 1X01
C11: 10nF; C0805
C12: 22uF; C0805
C15: 10uF; C0805
C22, C26: 10uF; 0805-NO@1
C23: 0.1uF; 0805-NO@1
GNDA: PINHD-1X1; 1X01
GNDB: PINHD-1X1; 1X01
IC7: MPM3610; QFN-20
IC8: 74AHCT1G125DBV; SOT23-5
PWMA: PINHD-1X1; 1X01
PWMB: PINHD-1X1; 1X01
PWRA: PINHD-1X1; 1X01
PWRB: PINHD-1X1; 1X01
Q4, Q6, Q8, Q10: DMG3415U-7; SOT23-WIDE
Q5, Q7, Q9: 2N2222; SOT23-BEC
R2: 19K1_0.1%; R0805
R4: 100K_1%; R0805
R7, R14, R19: 1K; 0603-NO
R11: 68k; R0805
R12, R13, R15, R16, R17, R18: 10K; 0603-NO
R20: 100K; 0805-NO
SG1: F/QMB

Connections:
9603_PWR: Q6.3 (D); also elsewhere on the board
+3V3: C26.1, Q10.2 (S), R20.1; also elsewhere on the board
+5V: C11.1, C12.1, C22.1, C23.1, IC7.7 (OUT), IC7.8 (OUT), IC7.9 (OUT), IC7.20 (OUT), IC8.5 (VCC), Q4.2 (S), Q6.2 (S), Q8.2 (S), R4.2, R12.1, R15.1, R16.1
A5: R7.1, R18.1; also elsewhere on the board
D2: R13.1, R19.1; also elsewhere on the board
D4: Q10.1 (G), R20.2; also elsewhere on the board
D5: IC8.2 (I); also elsewhere on the board
D7: R14.1, R17.1; also elsewhere on the board
D8: IC7.17 (EN); also elsewhere on the board
GND: BUZ-.1, C11.2, C12.2, C15.2, C22.2, C23.2, C26.2, GNDA.1, GNDB.1, IC7.3 (AGND), IC7.12 (GND), IC7.13 (GND), IC7.14 (GND), IC8.1 (OE), IC8.3 (GND), Q5.E, Q7.E, Q9.E, R2.1, R11.1, R13.2, R17.2, R18.2, SG1.- (+); also elsewhere on the board
unnamed: IC7.1 (FB), R2.2, R4.1
unnamed: Q7.B, R7.2
unnamed: Q6.1 (G), Q7.C, R16.2
unnamed: Q9.B, R19.2
unnamed: Q4.1 (G), Q5.C, R15.2
unnamed: Q5.B, R14.2
unnamed: Q8.1 (G), Q9.C, R12.2
unnamed: BUZ+.1, Q10.3 (D), SG1.+ (-)
unnamed: IC7.18 (AAM), R11.2
PWM: IC8.4 (O), PWMA.1, PWMB.1
SERVO_A_PWR: PWRA.1, Q4.3 (D)
SERVO_B_PWR: PWRB.1, Q8.3 (D)
VBAT: C15.1, IC7.16 (VIN); also elsewhere on the board

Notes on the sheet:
Servo A
Servo B
5V power switching for Servo A
5V power switching for Servo B
5V power switching for Iridium 9603
PWM level shifting (3V3 to 5V)
Sounder

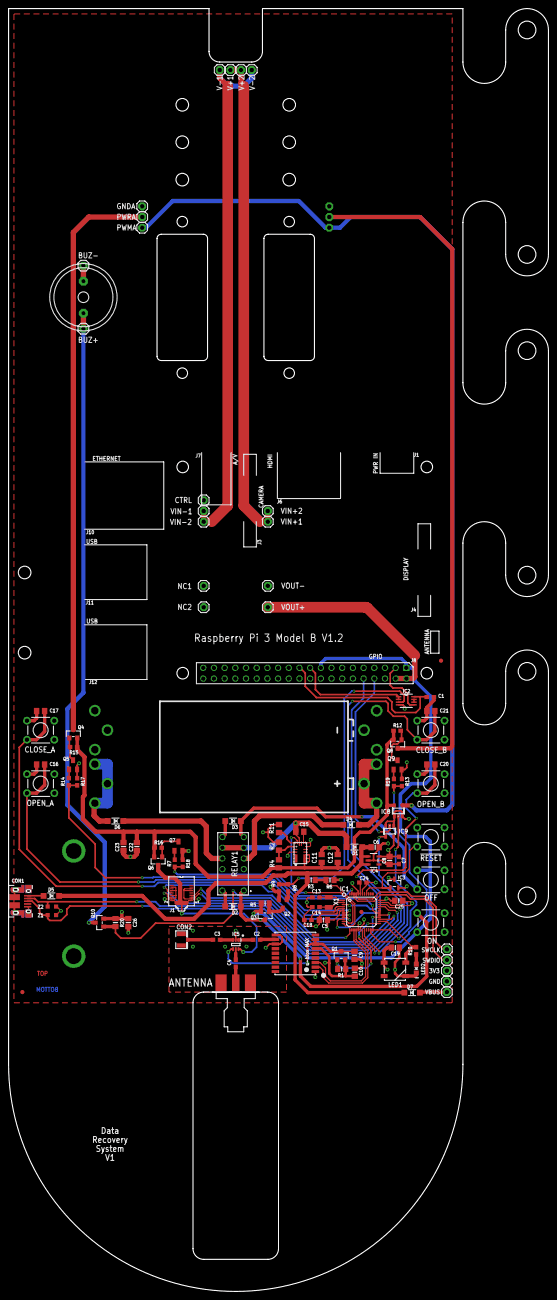
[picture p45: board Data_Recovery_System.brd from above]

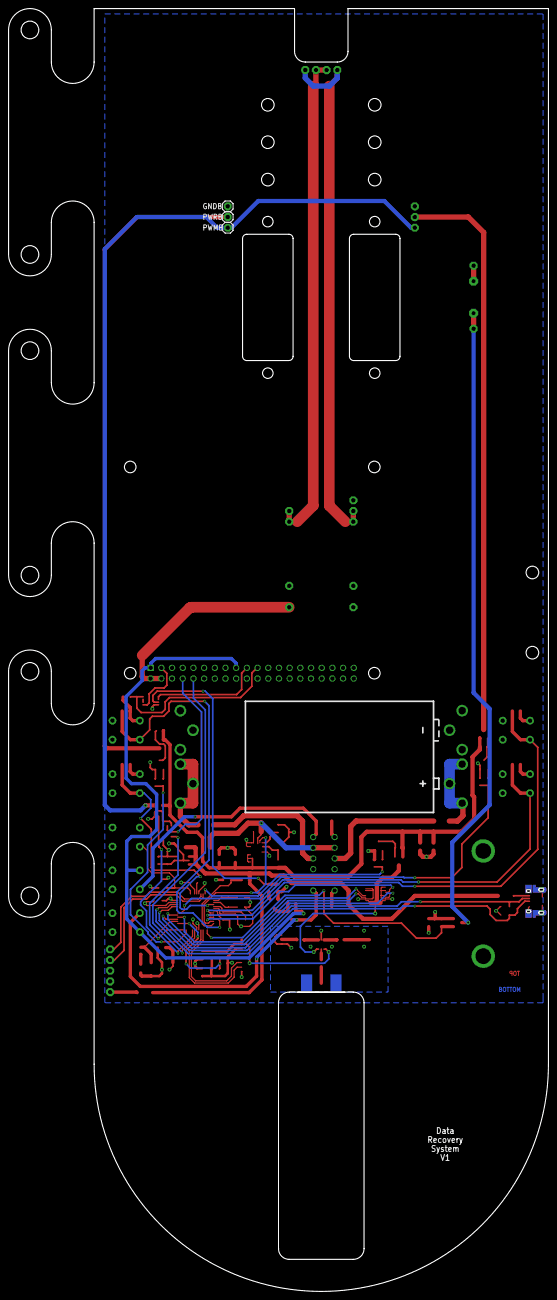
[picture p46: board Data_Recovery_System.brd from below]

Board: 4 copper layers, 128.3 x 304.8 mm, 123 parts (4 on the bottom side), 76 nets.

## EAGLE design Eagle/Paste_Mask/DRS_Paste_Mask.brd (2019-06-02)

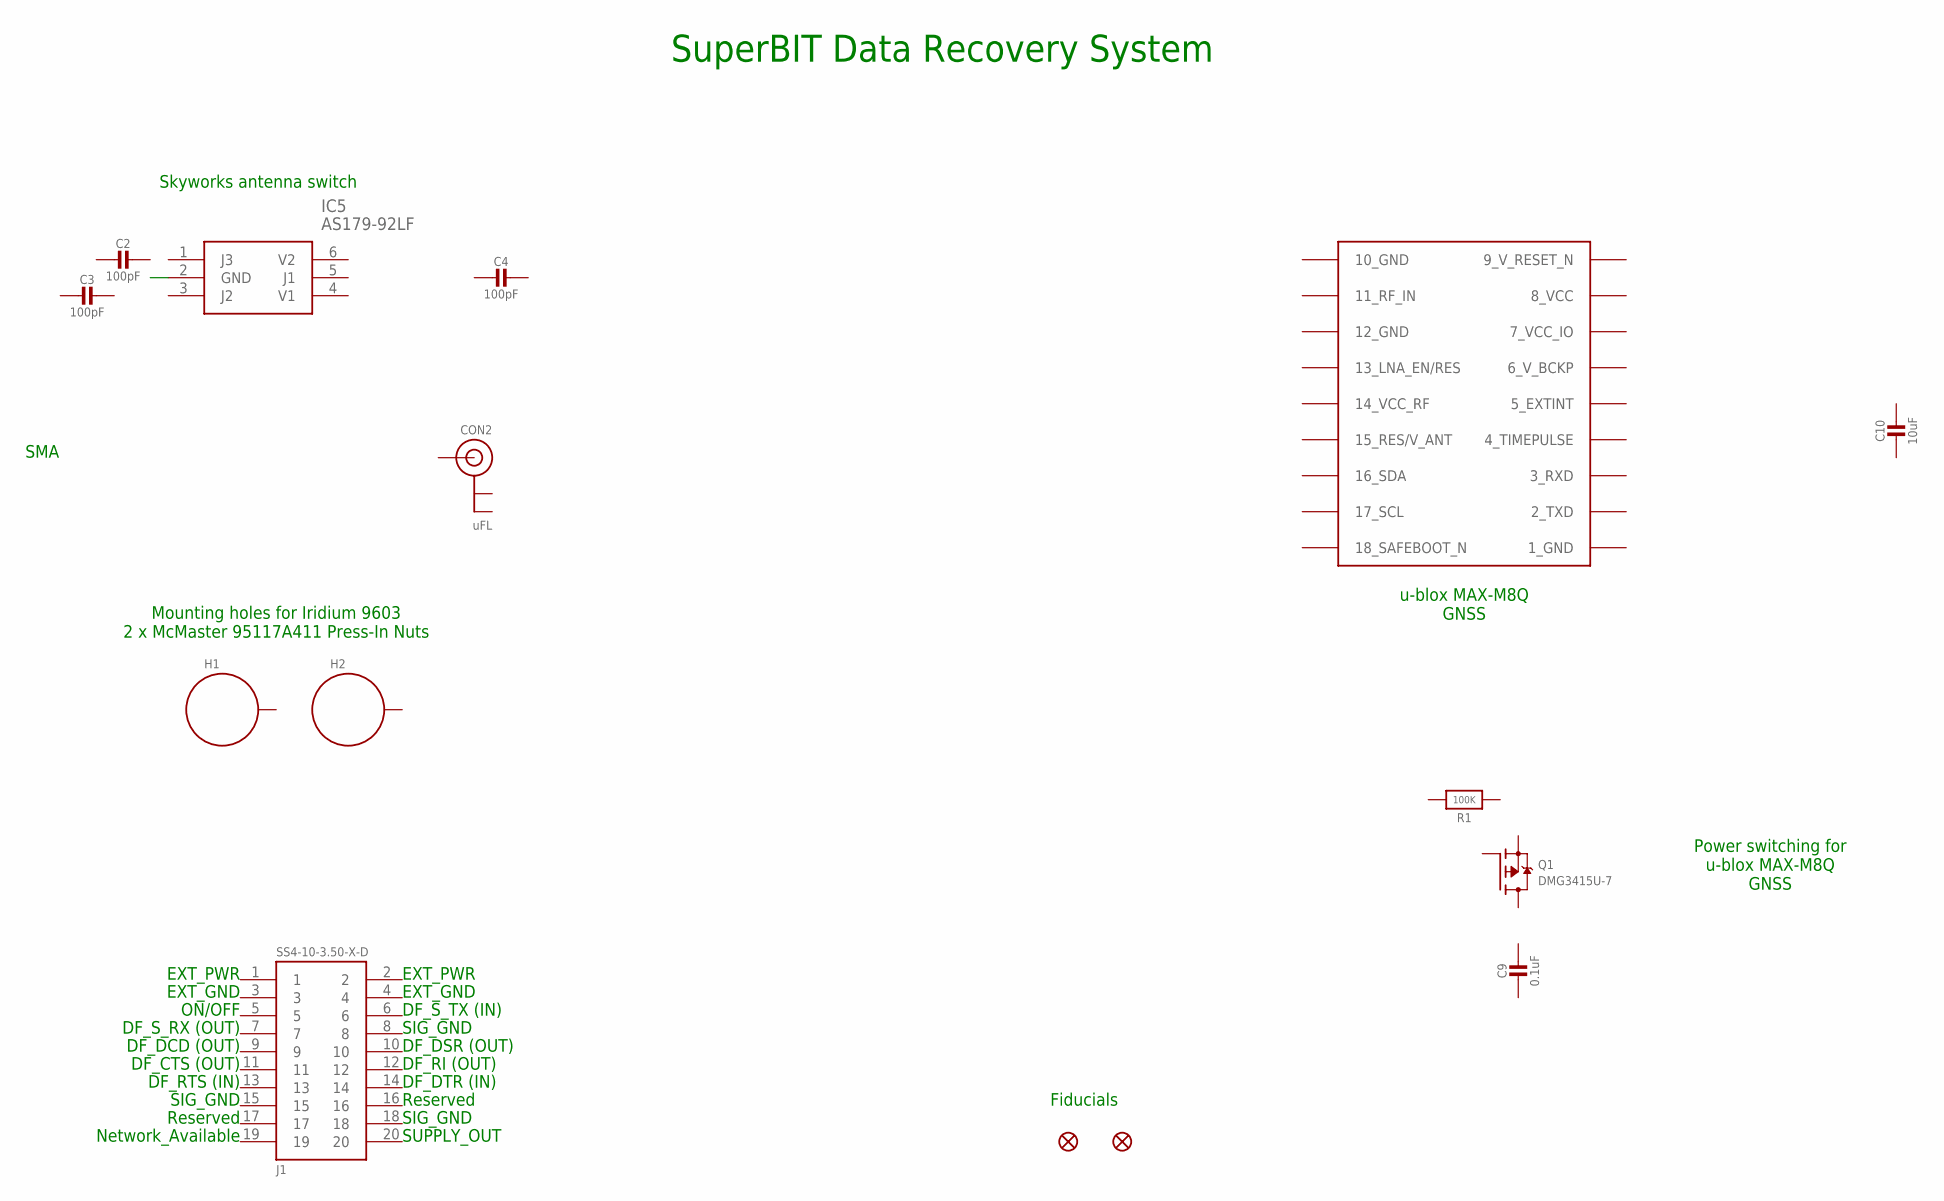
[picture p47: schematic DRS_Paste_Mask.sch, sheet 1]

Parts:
C2, C3, C4: 100pF; 0603-NO@1
C9: 0.1uF; 0805-NO@1
C10: 10uF; 0805-NO@1
CON2: uFL; U.FL
FD1, FD2: FIDUCIAL1X2; FIDUCIAL-1X2
H1, H2: STANDOFF_ELECTRICALMCMASTER-95117A411; STANDOFF-ELECTRICAL-MCMASTER-95117A411
IC5: AS179-92LF; SOT65P220X100-6N
IC6: MAX-M8
J1: SS4-10-3.50-X-D
Q1: DMG3415U-7; SOT23-WIDE
R1: 100K; 0805-NO

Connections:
1_GND: IC6.1_GND
7_VCC_IO: IC6.7_VCC_IO
8_VCC: IC6.8_VCC
9_V_RESET_N: IC6.9_RESET_N (9_V_RESET_N)
10_GND: IC6.10_GND
12_GND: IC6.12_GND

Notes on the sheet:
Mounting holes for Iridium 9603 2 x McMaster 95117A411 Press-In Nuts
SuperBIT Data Recovery System
EXT_PWR
EXT_GND
ON/OFF
DF_S_RX (OUT)
DF_DCD (OUT)
DF_CTS (OUT)
DF_RTS (IN)
SIG_GND
Reserved
Network_Available
DF_S_TX (IN)
DF_DSR (OUT)
DF_RI (OUT)
DF_DTR (IN)
SUPPLY_OUT
Fiducials
u-blox MAX-M8Q GNSS
Power switching for u-blox MAX-M8Q GNSS
Skyworks antenna switch
SMA

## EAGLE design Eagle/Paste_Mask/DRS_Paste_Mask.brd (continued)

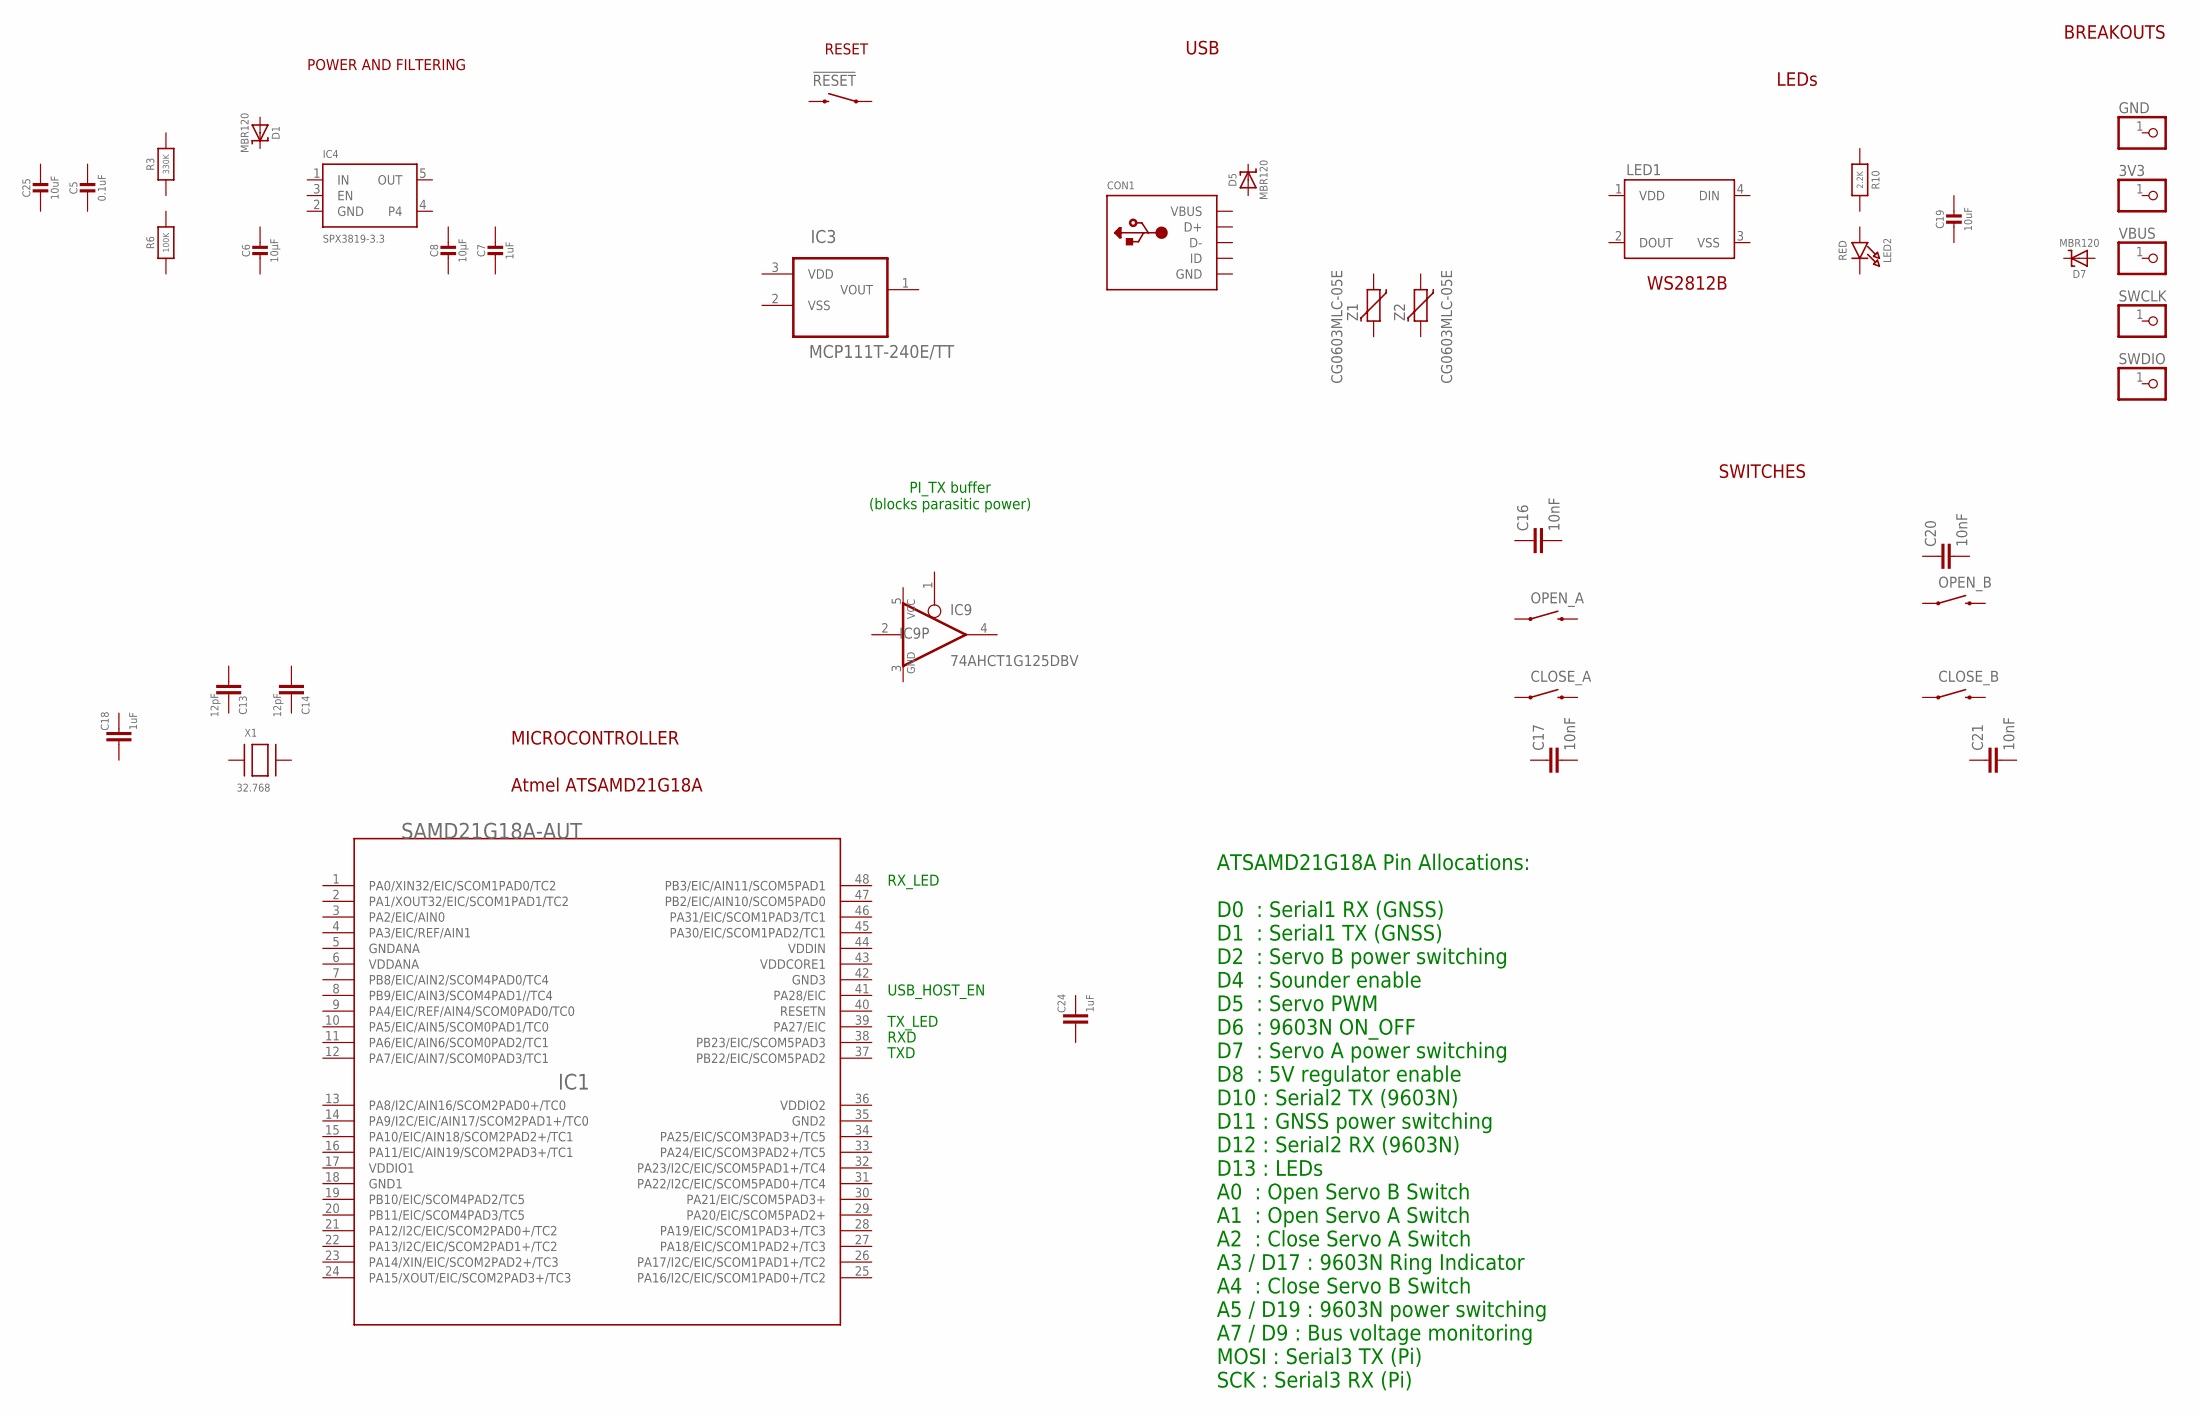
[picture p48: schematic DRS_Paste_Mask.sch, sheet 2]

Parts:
3V3: PINHD-1X1; 1X01
!RESET: SWITCH-MOMENTARY-2PTH; TACTILE-PTH
C5: 0.1uF; 0805-NO@1
C6, C8: 10µF; 0805-NO@1
C7: 1uF; 0603-NO@1
C13, C14: 12pF; C0603
C16, C17, C20, C21: 10nF; C0805
C18, C24: 1uF; C0603
C19, C25: 10uF; 0805-NO@1
CLOSE_A: SWITCH-MOMENTARY-2PTH; TACTILE-PTH
CLOSE_B: SWITCH-MOMENTARY-2PTH; TACTILE-PTH
CON1: MICROBUILDER_USBFCI_10103594_CORRECTED; MICROBUILDER_FCI_10103594_CORRECTED
D1, D5, D7: MBR120; SOD-123
GND: PINHD-1X1; 1X01
IC1: SAMD21G18A-AUT; TQFP48-7X7
IC3: MCP111T-240E/TT; SOT95P237X112-3N; MPN MCP111T-240E/TT
IC4: SPX3819-3.3; SOT23-5
IC9: 74AHCT1G125DBV; SOT23-5
LED1: WS2812B
LED2: RED; CHIPLED_0805_NOOUTLINE
OPEN_A: SWITCH-MOMENTARY-2PTH; TACTILE-PTH
OPEN_B: SWITCH-MOMENTARY-2PTH; TACTILE-PTH
R3: 330K; 0805-NO
R6: 100K; 0805-NO
R10: 2.2K; 0603-NO
SWCLK: PINHD-1X1; 1X01
SWDIO: PINHD-1X1; 1X01
VBUS: PINHD-1X1; 1X01
X1: 32.768; XTAL3215
Z1, Z2: CG0603MLC-05E; CT/CN0603

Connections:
GND: CON1.BASE@1 (GND), CON1.BASE@2 (GND), CON1.GND, CON1.SPRT@1 (GND), CON1.SPRT@2 (GND), CON1.SPRT@3 (GND), CON1.SPRT@4 (GND), IC4.2 (GND), IC9.3 (GND); also elsewhere on the board
GND1: IC1.18 (GND1)
GND2: IC1.35 (GND2)
GND3: IC1.42 (GND3)
GNDANA: IC1.5 (GNDANA)
IN: IC4.1 (IN)
VBUS: CON1.VBUS
VCC: IC9.5 (VCC); also elsewhere on the board
VDD: IC3.3 (VDD), LED1.1 (VDD)
VDDANA: IC1.6 (VDDANA)
VDDIN: IC1.44 (VDDIN)
VDDIO1: IC1.17 (VDDIO1)
VDDIO2: IC1.36 (VDDIO2)
VSS: IC3.2 (VSS), LED1.3 (VSS)

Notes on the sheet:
MICROCONTROLLER
USB_HOST_EN
TXD
RXD
TX_LED
RX_LED
Atmel ATSAMD21G18A
POWER AND FILTERING
RESET
USB
BREAKOUTS
LEDs
WS2812B
SWITCHES
ATSAMD21G18A Pin Allocations: D0 : Serial1 RX (GNSS) D1 : Serial1 TX (GNSS) D2 : Servo B power switching D4 : Sounder enable D5 : Servo PWM D6 : 9603N ON_OFF D7 : Servo A power switching D8 : 5V regulator enable D10 : Serial2 TX (9603N) D11 : GNSS power switching D12 : Serial2 RX (9603N) D13 : LEDs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
PI_TX buffer (blocks parasitic power)

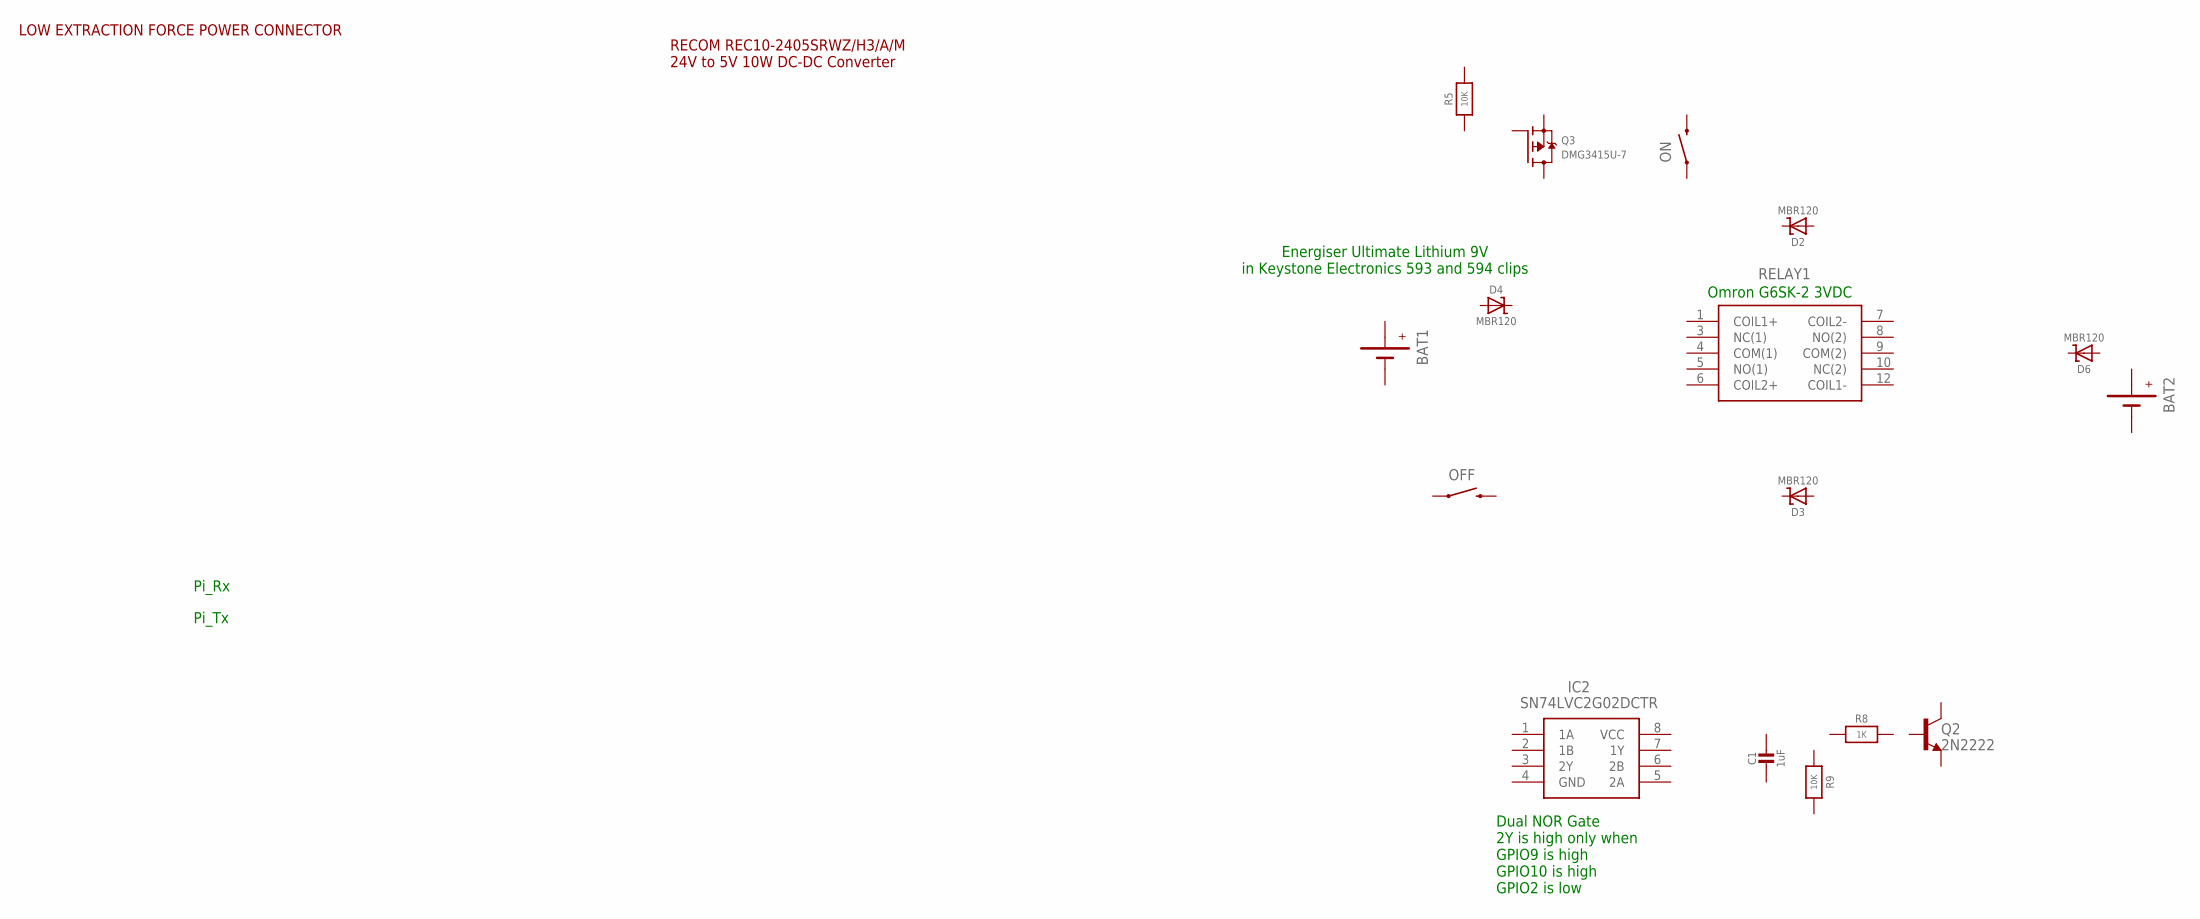
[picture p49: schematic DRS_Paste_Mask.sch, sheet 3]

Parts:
BAT1, BAT2: BATTERYBATTERY-9V-KEYSTONE-593-594; BATTERY-9V-KEYSTONE-593-594
C1: 1uF; 0603-NO@1
D2, D3, D4, D6: MBR120; SOD-123
IC2: SN74LVC2G02DCTR; SOP65P400X130-8N
OFF: SWITCH-MOMENTARY-2PTH; TACTILE-PTH
ON: SWITCH-MOMENTARY-2PTH; TACTILE-PTH
Q2: 2N2222; SOT23-BEC
Q3: DMG3415U-7; SOT23-WIDE
R5: 10K; 0805-NO
R8: 1K; 0603-NO
R9: 10K; 0603-NO
RELAY1: G6SK-2_DC5; G6SK2DC5

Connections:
+: BAT1.PWR (+), BAT1.PWR1 (+), BAT1.PWR2 (+), BAT2.PWR (+), BAT2.PWR1 (+), BAT2.PWR2 (+)
-: BAT1.GND (-), BAT1.GND1 (-), BAT1.GND2 (-), BAT2.GND (-), BAT2.GND1 (-), BAT2.GND2 (-)

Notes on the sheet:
Omron G6SK-2 3VDC
Energiser Ultimate Lithium 9V in Keystone Electronics 593 and 594 clips
LOW EXTRACTION FORCE POWER CONNECTOR
RECOM REC10-2405SRWZ/H3/A/M 24V to 5V 10W DC-DC Converter
Dual NOR Gate 2Y is high only when GPIO9 is high GPIO10 is high GPIO2 is low
Pi_Tx
Pi_Rx

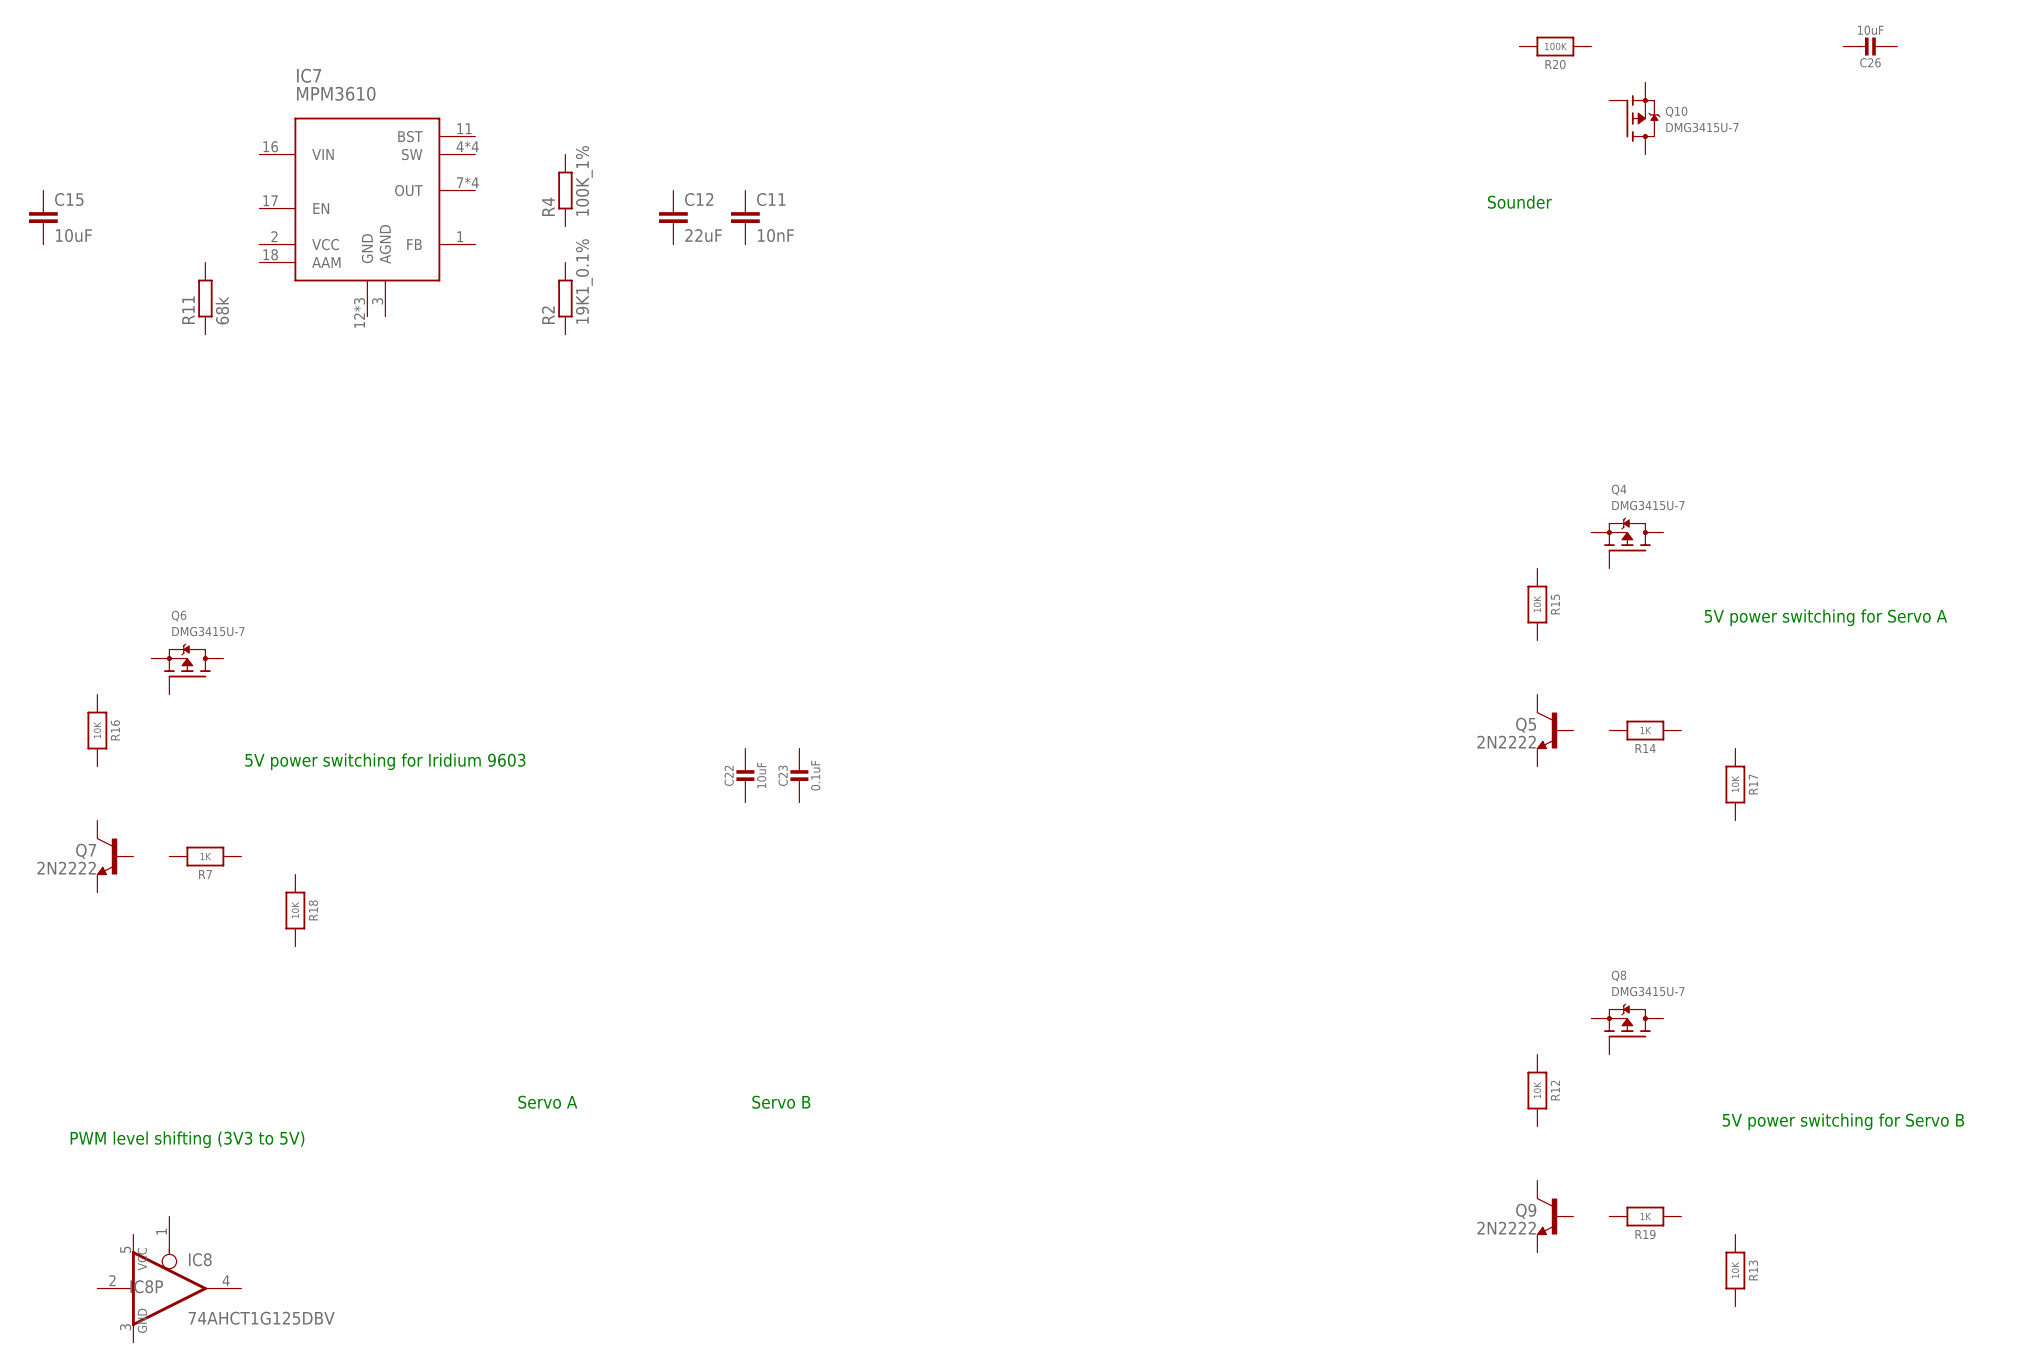
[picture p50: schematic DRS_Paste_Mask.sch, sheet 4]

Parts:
C11: 10nF; C0805
C12: 22uF; C0805
C15: 10uF; C0805
C22, C26: 10uF; 0805-NO@1
C23: 0.1uF; 0805-NO@1
IC7: MPM3610; QFN-20
IC8: 74AHCT1G125DBV; SOT23-5
Q4, Q6, Q8, Q10: DMG3415U-7; SOT23-WIDE
Q5, Q7, Q9: 2N2222; SOT23-BEC
R2: 19K1_0.1%; R0805
R4: 100K_1%; R0805
R7, R14, R19: 1K; 0603-NO
R11: 68k; R0805
R12, R13, R15, R16, R17, R18: 10K; 0603-NO
R20: 100K; 0805-NO

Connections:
GND: IC8.3 (GND); also elsewhere on the board
VCC: IC8.5 (VCC); also elsewhere on the board

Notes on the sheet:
Servo A
Servo B
5V power switching for Servo A
5V power switching for Servo B
5V power switching for Iridium 9603
PWM level shifting (3V3 to 5V)
Sounder

Board: 4 copper layers, 99 parts (1 on the bottom side), 6 nets, no tracks yet.

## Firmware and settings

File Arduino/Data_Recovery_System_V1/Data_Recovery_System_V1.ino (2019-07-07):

// ###########################
// # Data Recovery System V1 #
// ###########################

#define DRS1
//#define DRS2
//#define DRS3
//#define DRS4
//#define DRS5

// A hybrid of the Iridium9603NBeacon_V5 and Cut-Down_Device

// Uses Cristian Maglie's FlashStorage library to store the BEACON_INTERVAL and the servo settings
// https://github.com/cmaglie/FlashStorage
// BEACON_INTERVAL can be updated via an Iridium Mobile Terminated message

// With grateful thanks to Mikal Hart:
// Based on Mikal's IridiumSBD Beacon example: https://github.com/mikalhart/IridiumSBD
// Requires Mikal's TinyGPS library: https://github.com/mikalhart/TinyGPS
// and PString: http://arduiniana.org/libraries/pstring/

// With grateful thanks to:
// Adafruit: https://learn.adafruit.com/using-atsamd21-sercom-to-add-more-spi-i2c-serial-ports/creating-a-new-serial
// MartinL: https://forum.arduino.cc/index.php?topic=341054.msg2443086#msg2443086

// The Iridium_9603_Beacon PCB is based extensively on the Adafruit Feather M0 (Adalogger)
// https://www.adafruit.com/products/2796

// GNSS data provided by u-blox MAX-M8Q
// https://www.u-blox.com/en/product/max-m8-series

// WB2812B NeoPixel is connected to D13 in parallel with a standard Red LED (for the bootloader)
// Support for the WB2812B is provided by Adafruit:
// https://github.com/adafruit/Adafruit_NeoPixel

// Uses RTCZero to provide sleep functionality (on the M0)
// https://github.com/arduino-libraries/RTCZero

// With grateful thanks to CaveMoa for his SimpleSleepUSB example
// https://github.com/cavemoa/Feather-M0-Adalogger
// https://github.com/cavemoa/Feather-M0-Adalogger/tree/master/SimpleSleepUSB
// Note: you will need to close and re-open your serial monitor each time the M0 wakes up

// With thanks to David A. Mellis and Tom Igoe for the smoothing tutorial
// http://www.arduino.cc/en/Tutorial/Smoothing

// Stores both source and destination RockBLOCK serial numbers in flash.
// The default values are:
#define RB_destination 0 // Serial number of the destination RockBLOCK (int). Set to zero to disable RockBLOCK message forwarding

// Define default servo positions and RB_source
#ifdef DRS1
  // Default values for DRS1
  #define defServoOpenA 1869
  #define defServoClosedA 1227
  #define defServoOpenB 1937
  #define defServoClosedB 1513
  #define RB_source 11800
#endif
#ifdef DRS2
// Default values for DRS2
  #define defServoOpenA 1817
  #define defServoClosedA 1368
  #define defServoOpenB 1639
  #define defServoClosedB 1235
  #define RB_source 16366
#endif
#ifdef DRS3
// Default values for DRS3
  #define defServoOpenA 1744
  #define defServoClosedA 1280
  #define defServoOpenB 1651
  #define defServoClosedB 1273
  #define RB_source 16363
#endif
#ifdef DRS4
// Default values for DRS4
  #define defServoOpenA 1985
  #define defServoClosedA 1467
  #define defServoOpenB 1719
  #define defServoClosedB 1347
  #define RB_source 16365
#endif
#ifdef DRS5
// Default values for DRS5
  #define defServoOpenA 2035
  #define defServoClosedA 1457
  #define defServoOpenB 1833
  #define defServoClosedB 1482
  #define RB_source 16369
#endif

// ATSAMD21G18A Pin Allocations:
//
// D0  : Serial1 RX (GNSS)
// D1  : Serial1 TX (GNSS)
// D2  : Servo B power switching
// D4 / TCC1WO2 : Sounder enable
// D5 / TCC0WO5 : Servo PWM
// D6  : 9603N ON_OFF
// D7  : Servo A power switching
// D8  : 5V regulator enable
// D10 : Serial2 TX (9603N)
// D11 : GNSS power switching
// D12 : Serial2 RX (9603N)
// D13 : LEDs
// A0 / D14 : Open Servo B Switch
// A1 / D15 : Open Servo A Switch
// A2 / D16 : Close Servo A Switch
// A3 / D17 : 9603N Ring Indicator
// A4 / D18 : Close Servo B Switch
// A5 / D19 : 9603N power switching
// A7 / D9 : Bus voltage monitoring
// MOSI / D23 : Serial3 TX (Pi)
// SCK / D24 : Serial3 RX (Pi)

// !!! Ensure GPS_EN and Enable_9603N are not enabled at the same time !!!

// Red LED on D13 shows when the SAMD is in bootloader mode (LED will fade up/down)

// WB2812B on D13 indicates what the software is doing:
// Cyan: setServo mode (setServoA and setServoB)
// Blue: power is on; GNSS is powered up; waiting for the Go command (init_GPS and pi_echo)
// Magenta: Go command received; opening ServoA (drop and init)
// Blue: waiting for a GPS fix (start_GPS and read_GPS)
// White: Iridium transmit (start_9603)
// Green flash (2 seconds) indicates successful transmission
// Red flash (2+ seconds) entering sleep
// LED will flash Red after: Iridium transmission (successful or failure); low battery detected
// WB2812B blue LED has the highest forward voltage and is slightly dim at 3.3V. The red and green values are adapted accordingly (222 instead of 255).

static const int ServoB = 2; // Servo B Enable (Pull high to enable the servo)
static const int Sounder = 4; // Sounder Enable (Pull low to enable the sounder)
const uint8_t pwmPin = 5;
static const int IridiumSleepPin = 6; // Iridium 9603N ON/OFF
static const int ServoA = 7; // Servo A Enable (Pull high to enable the servo)
static const int enable5V = 8; // Enable the MPM3610 5V regulator (Pull high to enable 5V)
static const int GPS_EN = 11; // GNSS Enable (Pull low to enable the GNSS)
static const int ledPin = 13; // WB2812B + Red LED
static const int openSwitchB = 14;
static const int openSwitchA = 15;
static const int closeSwitchA = 16;
static const int ringIndicator = 17; // 9603N Ring Indicator
static const int closeSwitchB = 18;
static const int Enable_9603N = 19; // 9603N Enable (Pull high to enable power for the 9603N)

#include <IridiumSBD.h> // Requires V2: https://github.com/mikalhart/IridiumSBD
#include <TinyGPS.h> // NMEA parsing: http://arduiniana.org
#include <PString.h> // String buffer formatting: http://arduiniana.org

#include <Adafruit_NeoPixel.h> // Support for the WB2812B

#include <RTCZero.h> // M0 Real Time Clock
RTCZero rtc; // Create an rtc object

// Define how often messages are sent in MINUTES (max 1440)
// This is the _quickest_ messages will be sent. Could be much slower than this depending on:
// gnss fix time; Iridium timeout; etc.
// The default value will be overwritten with the one stored in Flash - if one exists
// The value can be changed via a Mobile Terminated message
int BEACON_INTERVAL = 2;

// Flash Storage
#include <FlashStorage.h>
typedef struct { // Define a struct to hold the flash variable(s)
  int PREFIX; // Flash storage prefix (0xB5); used to test if flash has been written to before 
  int INTERVAL; // Message interval in minutes
  // RockBLOCK source serial number: stored as an int; i.e. the RockBLOCK serial number of the 9603N attached to this beacon
  int RBSOURCE; 
  // RockBLOCK destination serial number: stored as an int; i.e. the RockBLOCK serial number of the 9603N you would like the messages delivered _to_
  int RBDESTINATION; // Set this to zero to disable RockBLOCK gateway message forwarding
  int servoOpenA; // Servo A PWM value for the open position
  int servoClosedA; // Servo A PWM value for the closed position
  int servoOpenB; // Servo B PWM value for the open position
  int servoClosedB; // Servo B PWM value for the closed position
  int GONE; // Flag to indicate if GoGoGo has been received (set loop_step to init not init_GPS after reset)
  int SOUNDER; // Flag to indicate if the sounder has been disabled via SBD message
  int CSUM; // Flash storage checksum; the modulo-256 sum of PREFIX to servoClosedB; used to check flash data integrity
} FlashVarsStruct;
FlashStorage(flashVarsMem, FlashVarsStruct); // Reserve memory for the flash variables
FlashVarsStruct flashVars; // Define the global to hold the variables
int RBSOURCE = RB_source;
int RBDESTINATION = RB_destination;

// Serial2 pin and pad definitions (in Arduino files Variant.h & Variant.cpp)
#define PIN_SERIAL2_RX       (34ul)               // Pin description number for PIO_SERCOM on D12
#define PIN_SERIAL2_TX       (36ul)               // Pin description number for PIO_SERCOM on D10
#define PAD_SERIAL2_TX       (UART_TX_PAD_2)      // SERCOM pad 2 (SC1PAD2)
#define PAD_SERIAL2_RX       (SERCOM_RX_PAD_3)    // SERCOM pad 3 (SC1PAD3)
// Instantiate the Serial2 class
Uart Serial2(&sercom1, PIN_SERIAL2_RX, PIN_SERIAL2_TX, PAD_SERIAL2_RX, PAD_SERIAL2_TX);
HardwareSerial &ssIridium(Serial2);

// Serial3 pin and pad definitions (in Arduino files Variant.h & Variant.cpp)
// Serial3 Tx : MOSI (Digital Pin 23, Port B Pin 10, SERCOM4 Pad 2)
// Serial3 Rx : SCK (Digital Pin 24, Port B Pin 11, SERCOM4 Pad 3)
#define PIN_SERIAL3_RX       (24ul)               // Pin description number for PIO_SERCOM on D24
#define PIN_SERIAL3_TX       (23ul)               // Pin description number for PIO_SERCOM on D23
#define PAD_SERIAL3_TX       (UART_TX_PAD_2)      // SERCOM4 Pad 2 (SC4PAD2)
#define PAD_SERIAL3_RX       (SERCOM_RX_PAD_3)    // SERCOM4 Pad 3 (SC4PAD3)
// Instantiate the Serial3 class
Uart Serial3(&sercom4, PIN_SERIAL3_RX, PIN_SERIAL3_TX, PAD_SERIAL3_RX, PAD_SERIAL3_TX);
HardwareSerial &ssPi(Serial3);

#define ssGPS Serial1 // Use M0 Serial1 to interface to the MAX-M8Q

// Leave the "#define GALILEO" uncommented to use: GPS + Galileo + GLONASS + SBAS
// Comment the "#define GALILEO" out to use the default u-blox M8 GNSS: GPS + SBAS + QZSS + GLONASS
#define GALILEO

// Set Nav Mode to Portable
static const uint8_t setNavPortable[] = {
  0xB5, 0x62, 0x06, 0x24, 0x24, 0x00, 0x01, 0x00, 0x00, 0x03, 0x00, 0x00, 0x00, 0x00, 0x10, 0x27, 0x00, 0x00, 
  0x05, 0x00, 0xFA, 0x00, 0xFA, 0x00, 0x64, 0x00, 0x2C, 0x01, 0x00, 0x00, 0x00, 0x00, 0x00, 0x00, 0x00, 0x00, 
  0x03, 0x00, 0x00, 0x00, 0x00, 0x00 };

// Set Nav Mode to Airborne <1G
static const uint8_t setNavAir[] = {
  0xB5, 0x62, 0x06, 0x24, 0x24, 0x00, 0x01, 0x00, 0x06, 0x03, 0x00, 0x00, 0x00, 0x00, 0x10, 0x27, 0x00, 0x00, 
  0x05, 0x00, 0xFA, 0x00, 0xFA, 0x00, 0x64, 0x00, 0x2C, 0x01, 0x00, 0x00, 0x00, 0x00, 0x00, 0x00, 0x00, 0x00, 
  0x03, 0x00, 0x00, 0x00, 0x00, 0x00 };
static const int len_setNav = 42;

// Set NMEA Config
// Set trackFilt to 1 to ensure course (COG) is always output
// Set Main Talker ID to 'GP' to avoid having to modify TinyGPS
static const uint8_t setNMEA[] = {
  0xb5, 0x62, 0x06, 0x17, 0x14, 0x00, 0x20, 0x40, 0x00, 0x02, 0x00, 0x00, 0x00, 0x00, 0x00, 0x01, 0x01, 0x01,
  0x00, 0x00, 0x00, 0x00, 0x00, 0x00, 0x00, 0x00 };
static const int len_setNMEA = 26;

// Set GNSS Config to GPS + Galileo + GLONASS + SBAS (Causes the M8 to restart!)
static const uint8_t setGNSS[] = {
  0xb5, 0x62, 0x06, 0x3e, 0x3c, 0x00,
  0x00, 0x20, 0x20, 0x07,
  0x00, 0x08, 0x10, 0x00, 0x01, 0x00, 0x01, 0x01,
  0x01, 0x01, 0x03, 0x00, 0x01, 0x00, 0x01, 0x01,
  0x02, 0x08, 0x08, 0x00, 0x01, 0x00, 0x01, 0x01,
  0x03, 0x08, 0x10, 0x00, 0x00, 0x00, 0x01, 0x01,
  0x04, 0x00, 0x08, 0x00, 0x00, 0x00, 0x01, 0x03,
  0x05, 0x00, 0x03, 0x00, 0x00, 0x00, 0x01, 0x05,
  0x06, 0x04, 0x0e, 0x00, 0x01, 0x00, 0x01, 0x01 };
static const int len_setGNSS = 66;

// Clear Stored Configuration
// Clears msgConf, navConf, rxmConf
static const uint8_t clearConf[] = {
  0xb5, 0x62, 0x06, 0x09, 0x0C, 0x00,
  0x1A, 0x00, 0x00, 0x00, 0x00, 0x00, 0x00, 0x00, 0x00, 0x00, 0x00, 0x00 };
// Save Configuration
// Saves msgConf, navConf, rxmConf
static const uint8_t saveConf[] = {
  0xb5, 0x62, 0x06, 0x09, 0x0C, 0x00,
  0x00, 0x00, 0x00, 0x00, 0x1A, 0x00, 0x00, 0x00, 0x00, 0x00, 0x00, 0x00 };
// Load Configuration
// Loads msgConf, navConf, rxmConf
static const uint8_t loadConf[] = {
  0xb5, 0x62, 0x06, 0x09, 0x0C, 0x00,
  0x00, 0x00, 0x00, 0x00, 0x00, 0x00, 0x00, 0x00, 0x1A, 0x00, 0x00, 0x00 };
static const int len_Conf = 18;

IridiumSBD isbd(ssIridium, IridiumSleepPin); // This should disable the 9603
TinyGPS tinygps;
long iterationCounter = 0; // Increment each time a transmission is attempted

//#define NoLED // Uncomment this line to disable the LED
#define swap_red_green // Uncomment this line if your WB2812B has red and green reversed
#ifdef swap_red_green
  Adafruit_NeoPixel pixels = Adafruit_NeoPixel(1, ledPin, NEO_GRB + NEO_KHZ800); // GRB WB2812B
#else
  Adafruit_NeoPixel pixels = Adafruit_NeoPixel(1, ledPin, NEO_RGB + NEO_KHZ800); // RGB WB2812B
#endif
#define LED_Brightness 32 // 0 - 255 for WB2812B

#define GPS_ON LOW
#define GPS_OFF HIGH
#define SOUNDER_ON LOW
#define SOUNDER_OFF HIGH
#define SERVO_ON HIGH
#define SERVO_OFF LOW
#define IRIDIUM_ON HIGH
#define IRIDIUM_OFF LOW
#define FIVE_V_ON HIGH
#define FIVE_V_OFF LOW

#define VBUS A7 // Bus voltage analog pin
#define VBAT_LOW 6.5 // Minimum battery voltage for MPM3610

// Loop Steps
#define setServoA     0
#define setServoB     1
#define init_GPS      2
#define pi_echo       3
#define drop          4
#define init          5
#define start_GPS     6
#define read_GPS      7
#define start_9603    8
#define zzz           9
#define wake          10
#define close_a       11
#define open_a        12
#define close_b       13
#define open_b        14

// Variables used by Loop
int year;
byte month, day, hour, minute, second, hundredths;
unsigned long dateFix, locationFix;
float latitude, longitude;
long altitude;
float speed;
short satellites;
long course;
long hdop;
bool fixFound = false;
bool charsSeen = false;
int loop_step = init_GPS;
float vbat = 9.0;
unsigned long tnow;
bool open_servo_B_flag = false;

// Servo Position:
// Min Position = 900
// Mid Position = 1500
// Max Position = 2100
const int minServo = 900;
const int midServo = 1500;
const int maxServo = 2100;
int PWM = midServo;
int servoOpenA = midServo;
int servoClosedA = midServo;
int servoOpenB = midServo;
int servoClosedB = midServo;

// Drop countdown (secs)
#define countdown 30

// Storage for the average voltage during Iridium callbacks
const int numReadings = 25;   // number of samples
int readings[numReadings];    // the readings from the analog input
int readIndex = 0;            // the index of the current reading
long int total = 0;           // the running total
int latest_reading = 0;       // the latest reading
int average_reading = 0;      // the average reading

// IridiumSBD Callbacks
bool ISBDCallback()
{
#ifndef NoLED
  // 'Flash' the LED
  if ((millis() / 1000) % 2 == 1) {
    LED_dim_white();
  }
  else {
    LED_white();
  }
#endif

  // Check the 'battery' voltage now we are drawing current for the 9603
  // If voltage is low, stop Iridium send
  // Average voltage over numReadings to smooth out any short dips
  get_vbat_smooth();

  if (vbat < VBAT_LOW) {
    Serial.print("***!!! LOW VOLTAGE (ISBDCallback) ");
    Serial.print(vbat,2);
    Serial.println("V !!!***");
    return false; // Returning false causes IridiumSBD to terminate
  }
  else {     
    return true;
  }

  delay(1);
}
// V2 console and diagnostic callbacks (replacing attachConsole and attachDiags)
void ISBDConsoleCallback(IridiumSBD *device, char c) { Serial.write(c); }
void ISBDDiagsCallback(IridiumSBD *device, char c) { Serial.write(c); }

// Interrupt handler for SERCOM1 (essential for Serial2 comms)
void SERCOM1_Handler()
{
  Serial2.IrqHandler();
}

// Interrupt handler for SERCOM4 (essential for Serial3 comms)
void SERCOM4_Handler()
{
  Serial3.IrqHandler();
}
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
void loop()
{
  unsigned long loopStartTime = millis();

  switch(loop_step) {

    case setServoA:
    {
      // Power up the servo
      digitalWrite(enable5V, FIVE_V_ON);
      digitalWrite(ServoA, SERVO_ON);

      bool decOne = false; // Flag to indicate that the PWM should be decremented by one
      bool incOne = false; // Flag to indicate that the PWM should be incremented by one

      int plusSwitchState = digitalRead(closeSwitchB); // Read the plus switch state
      int minusSwitchState = digitalRead(openSwitchB); // Read the minus switch state
    
      if ((plusSwitchState == 0) and (minusSwitchState == 1)) {
        // If only the plusSwitch is low (pressed) decrement the PWM value
        decOne = true;
      }
      else if ((plusSwitchState == 1) and (minusSwitchState == 0)) {
        // If only the minusSwitch is low (pressed) increment the PWM value
        incOne = true;
      }
      // If neither or both switches are pressed, do nothing
      
      if ((incOne == true) || (decOne == true)) {
        // If either switch was pressed
        if (incOne == true) {
          if (PWM < maxServo) {
            PWM = PWM + 1;
          }
        }
        else {
          if (PWM > minServo) {
            PWM = PWM - 1;
          }
        }
      }

      // Update the servo PWM
      REG_TCC0_CCB1 = PWM; // TCC0 CCB1 - change the servo PWM on D5
      while(TCC0->SYNCBUSY.bit.CCB1);

      // Wait (blocking!!)
      delay(10);
        
      bool updateFlash = false; // Flag to indicate that the flash storage should be updated

      int openSwitchState = digitalRead(openSwitchA); // Read the open switch state
      int closeSwitchState = digitalRead(closeSwitchA); // Read the close switch state
    
      if ((openSwitchState == 0) and (closeSwitchState == 1)) {
        // If only the openSwitch is low (pressed) update servoOpen
        updateFlash = true;
        servoOpenA = PWM;
      }
      else if ((openSwitchState == 1) and (closeSwitchState == 0)) {
        // If only the closeSwitch is low (pressed) update servoClose
        updateFlash = true;
        servoClosedA = PWM;
      }
      // If neither or both switches are pressed, do nothing
        
      if (updateFlash == true) {
        // If either switch was pressed, update flash memory
        flashVars.PREFIX = 0xB5; // Initialise the prefix (hopefully redundant!)
        flashVars.servoOpenA = servoOpenA; // Update the ServoA settings
        flashVars.servoClosedA = servoClosedA;
        int csum = flashVars.PREFIX + flashVars.INTERVAL + flashVars.RBSOURCE + flashVars.RBDESTINATION + flashVars.servoOpenA + flashVars.servoClosedA + flashVars.servoOpenB + flashVars.servoClosedB + flashVars.GONE + flashVars.SOUNDER; // Update the checksum
        csum = csum & 0xff;
        flashVars.CSUM = csum;
        flashVarsMem.write(flashVars); // Write the flash variables

        LED_green();
        delay(2000); // Wait (blocking!)
        LED_cyan();
        
        // Wait until both open and close switches have been released
        while ((openSwitchState == 0) || (openSwitchState == 0)) {
          openSwitchState = digitalRead(openSwitchA); // Read the open switch state
          closeSwitchState = digitalRead(closeSwitchA); // Read the close switch state
        }
      }
    }
    break;

    case setServoB:
    {
      // Power up the servo
      digitalWrite(enable5V, FIVE_V_ON);
      digitalWrite(ServoB, SERVO_ON);

      bool decOne = false; // Flag to indicate that the PWM should be decremented by one
      bool incOne = false; // Flag to indicate that the PWM should be incremented by one

      int plusSwitchState = digitalRead(closeSwitchA); // Read the plus switch state
      int minusSwitchState = digitalRead(openSwitchA); // Read the minus switch state
    
      if ((plusSwitchState == 0) and (minusSwitchState == 1)) {
        // If only the plusSwitch is low (pressed) decrement the PWM value
        decOne = true;
      }
      else if ((plusSwitchState == 1) and (minusSwitchState == 0)) {
        // If only the minusSwitch is low (pressed) increment the PWM value
        incOne = true;
      }
      // If neither or both switches are pressed, do nothing
      
      if ((incOne == true) || (decOne == true)) {
        // If either switch was pressed
        if (incOne == true) {
          if (PWM < maxServo) {
            PWM = PWM + 1;
          }
        }
        else {
          if (PWM > minServo) {
            PWM = PWM - 1;
          }
        }
      }

      // Update the servo PWM
      REG_TCC0_CCB1 = PWM; // TCC0 CCB1 - change the servo PWM on D5
      while(TCC0->SYNCBUSY.bit.CCB1);

      // Wait (blocking!!)
      delay(10);
        
      bool updateFlash = false; // Flag to indicate that the flash storage should be updated

      int openSwitchState = digitalRead(openSwitchB); // Read the open switch state
      int closeSwitchState = digitalRead(closeSwitchB); // Read the close switch state
    
      if ((openSwitchState == 0) and (closeSwitchState == 1)) {
        // If only the openSwitch is low (pressed) update servoOpen
        updateFlash = true;
        servoOpenB = PWM;
      }
      else if ((openSwitchState == 1) and (closeSwitchState == 0)) {
        // If only the closeSwitch is low (pressed) update servoClose
        updateFlash = true;
        servoClosedB = PWM;
      }
      // If neither or both switches are pressed, do nothing
        
      if (updateFlash == true) {
        // If either switch was pressed, update flash memory
        flashVars.PREFIX = 0xB5; // Initialise the prefix (hopefully redundant!)
        flashVars.servoOpenB = servoOpenB; // Update the ServoB settings
        flashVars.servoClosedB = servoClosedB;
        int csum = flashVars.PREFIX + flashVars.INTERVAL + flashVars.RBSOURCE + flashVars.RBDESTINATION + flashVars.servoOpenA + flashVars.servoClosedA + flashVars.servoOpenB + flashVars.servoClosedB + flashVars.GONE + flashVars.SOUNDER; // Update the checksum
        csum = csum & 0xff;
        flashVars.CSUM = csum;
        flashVarsMem.write(flashVars); // Write the flash variables
        
        LED_green();
        delay(2000); // Wait (blocking!)
        LED_cyan();
        
        // Wait until both open and close switches have been released
        while ((openSwitchState == 0) || (openSwitchState == 0)) {
          openSwitchState = digitalRead(openSwitchB); // Read the open switch state
          closeSwitchState = digitalRead(closeSwitchB); // Read the close switch state
        }
      }
    }
    break;

    case init_GPS:
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

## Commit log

2019-06-02 Work in progress
    [DRS_Paste_Mask.brd, DRS_Paste_Mask.sch, Data_Recovery_System.brd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]
2019-06-14 More added - but still work in progress
    [Data_Recovery_System_BOM.xlsx]
2019-06-14 Added PCB.md
2023-10-02 New Zealand SPB additions - files for 3D printing
    Inventor or SCAD files for 3D printing/milling the adapted case, crown release mechanism, and heatsink used in the 2023 flight from New Zealand.
    [ASSEM.SLDASM, CableMount.SLDPRT, Case.SLDPRT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]

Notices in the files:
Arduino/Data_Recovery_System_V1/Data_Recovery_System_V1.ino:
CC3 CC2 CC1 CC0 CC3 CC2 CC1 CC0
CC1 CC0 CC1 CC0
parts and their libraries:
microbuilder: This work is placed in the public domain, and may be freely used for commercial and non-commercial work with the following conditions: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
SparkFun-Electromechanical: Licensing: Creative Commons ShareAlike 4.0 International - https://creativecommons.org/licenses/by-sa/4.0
